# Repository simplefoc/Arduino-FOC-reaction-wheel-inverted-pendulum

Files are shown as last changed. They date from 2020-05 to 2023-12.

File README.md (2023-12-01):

# Arduino field oriented control (FOC) reaction wheel inverted pendulum   



This is a project of designing and controlling the reaction wheel inverted pendulum based entirely on Arduino [SimpleFOC library and SimpleFOC shield](https://github.com/simplefoc/Arduino-FOC). 

<p align="center">
    
    
</p>

This is a very fun project in many ways, and it is intended:
- Students in search for a good testing platform for their advanced algorithms
- Everyone with a bit of free time and a motivation to create something cool :D

### YouTube demonstration video :D
<p align="center">
<a href="https://youtu.be/Ih-izQyXJCI">

</a>
</p>

But for me, the most exciting part of this project was the ability to use the Field Oriented Control algorithm. 
**The main benefits of using the BLDC motor in this project are:**
-  High torque to weight ratio
   - The lighter the better
-  Lots of torque for low angular velocities
   - No need to spin the motor to very high RPM to achieve high torques
-  No gearboxes and backlash
   - Very smooth operation = very stable pendulum

So far, FOC has been restricted to high-end applications due to the complexity and the cost of the hardware mostly, but also due to the lack of user-friendly, well documented software. Therefore I am very happy to show you the projects like this one, which directly benefit the FOC algorithm and BLDC motors and encourage you to use these techniques in your projects as well. One of the very simple ways of starting (demonstrated in this video) is using the [SimpleFOC library and SimpleFOC shield](https://github.com/
/Arduino-FOC). 

## Readme structure 
- [What are the necessary components?](#what-are-the-necessary-components)
  - [3D printed parts](#3d-printed-parts)
  - [Hardware parts](#hardware-parts)
  - [Electrical components](#electrical-components)
    - [BLDC motor](#bldc-motor)
    - [Position sensors](#position-sensors)
    - [BLDC driver](#bldc-driver)
  - [Table mount](#table-mount)
- [Connecting all the components](#connecting-all-the-components)
  - [Encoder 1 (motor)](#encoder-1-motor)
  - [Encoder 2 (pendulum)](#encoder-2-pendulum)
  - [Motor](#motor)
- [Arduino code](#arduino-code)
  - [Encoder 1 (motor) code](#encoder-1-motor-code)
  - [Encoder 2 (pendulum) code](#encoder-2-pendulum-code)
  - [Motor code](#motor-code)
  - [Control algorithm code](#control-algorithm-code)
      - [Stabilization](#stabilization)
      - [Swing-up](#swing-up)
      - [The integration](#the-integration)
  - [Full Arduino code](#full-arduino-code)
- [Contact](#contact)

# What are the necessary components?
Due to the using of the brushless motor and the SimpleFOC shield, this might be one of the simplest hardware setups of the reaction wheel inverted pendulum there is.
<p align="center">
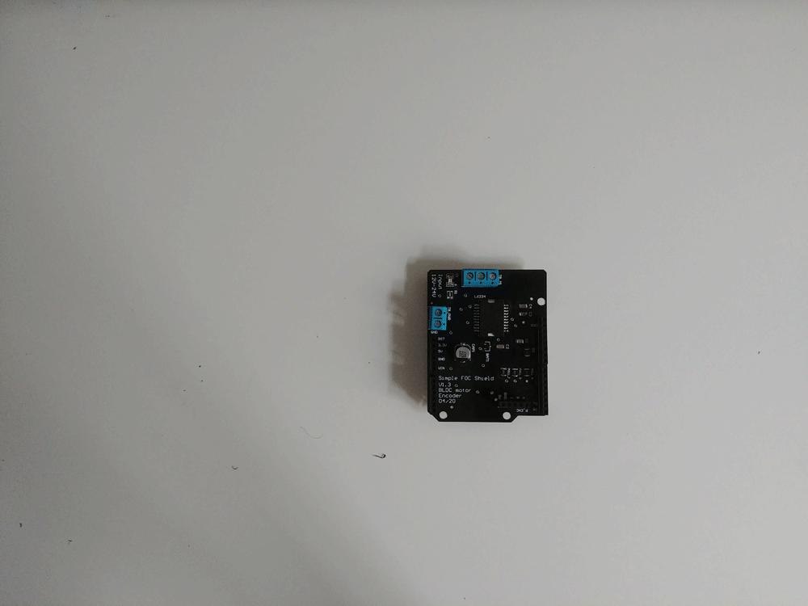
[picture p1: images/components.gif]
    
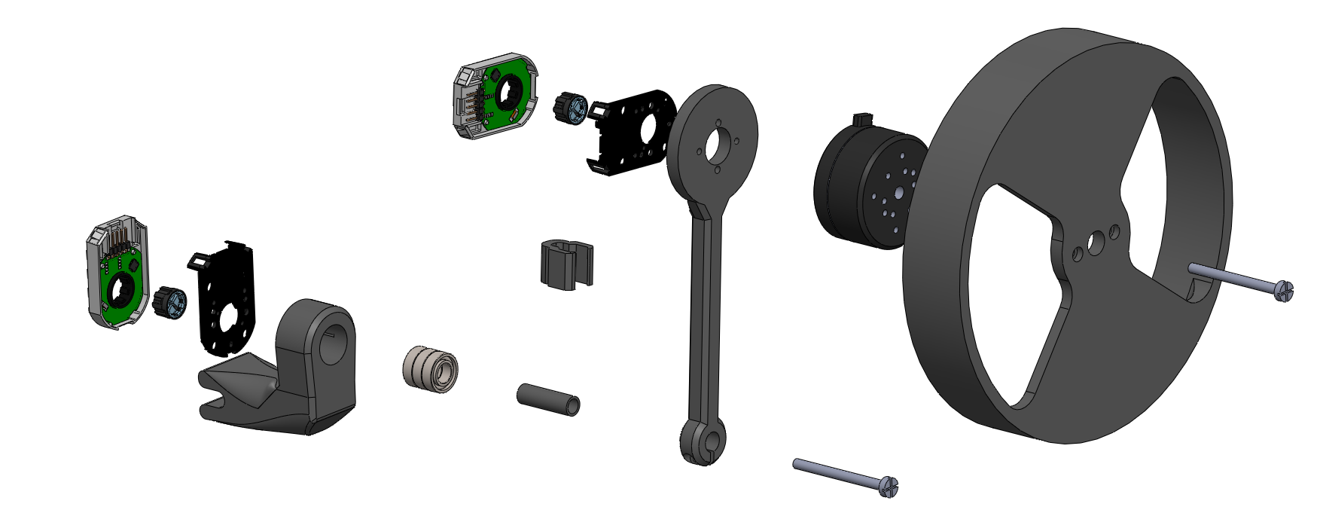
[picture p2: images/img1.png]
    
</p>

## 3D printed parts
This pendulum project has three 3d printed parts. You can find them in the `CAD files > STL` directory. They are:
- inertia wheel (`reaction_wheel.stl`)
    - infill: `70%`
    - layer hight: `<0.12mm`
    - it should be printed as precise as possible (to reduce the vibrations)
    - mass: `100g`
- pendulum arm (`pendulum_arm.stl`) 
    - infill: `50-70%`
    - layer hight: `0.12-0.2mm`
    - no need for too much precision, only the strength
    - mass: `20g`
- base (`bottpm_swingup.stl`)
    - infill: `70%`
    - layer hight: `<0.12`
    - due to the bearings needs to be pretty precise
    - mass: `60g`
- cable holder (`cable_holder.stl`) - *optional*

I have printed the pendulum in the PETG filament but there should be no real difference in using PLA or ABS filaments, this is just what I had in hand at the moment.

You will also find all the CAD files used in this project in the `CAD files` folder. I have included the Solidworks 2016 parts and the full assembly. Additionally all the parts are exported to STEP format for easier porting to the other CAD IDEs.

> Beware: 
I have designed the holes on the pendulum arm and the wheel to match perfectly the motor the encoders I was using, so please check the dimensions of your motors and encoder holes before printing :D

If you would prefer some other CAD format, let me know, maybe I can export it differently. 

## Hardware parts
All of the mechanical hardware is very simple and can be bought in any hardware store. If you prefer to buy it online, I have included links to the Ebay products you could use. 

Component | Description | Link | Price
---- | ---- | ---- | ----
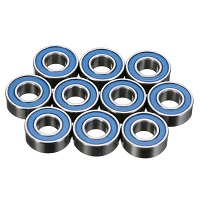
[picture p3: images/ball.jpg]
 | Ball bearing <br> 8x16x5mm <br> 3x | [Ebay](https://www.ebay.com/itm/608-623-625-688zz-Double-sided-Metal-Sealed-Deep-Groove-Ball-Bearing-High-Speed/223959673454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) | 3$
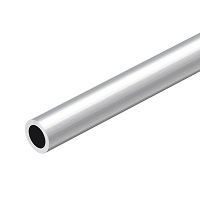
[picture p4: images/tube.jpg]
 | Aluminum tube <br> diameter: 8mm  <br> length: 30mm | [Ebay](https://www.ebay.com/itm/Aluminum-Tube-in-various-diam-and-many-lengths/122904111733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) | 3$
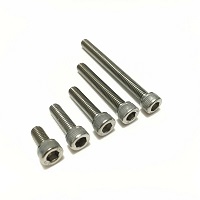
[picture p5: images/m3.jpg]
 |M3 screws<br> 7pcs <br> M3x10mm | [Ebay](https://www.ebay.com/itm/M2-M2-5-M3-M4-M5-M6-M8-Stainless-Steel-Metric-Hex-Socket-Head-Cap-Screws-Bolt/123439613021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) | 2$
 | M4 screws & nuts<br> 2pcs <br> M4x50mm | [Ebay](https://www.ebay.com/itm/M2-M2-5-M3-M4-M5-M6-M8-Stainless-Steel-Metric-Hex-Socket-Head-Cap-Screws-Bolt/123439613021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) | 4$

## Electrical components
### BLDC motor
Unfortunately the BLDC motor I was using in my video is an old version of the [iPower GM4108](https://shop.iflight-rc.com/index.php?route=product/product&product_id=217&search=GM4108H-120T) motor which is not available anymore to buy, in any case I was not able to find a website that would sell them. 
The good news is that you can use basically any other gimbal motor in that class with only minor modifications, mostly in the CAD parts - change the mounting holes positions. Some of the motors I was able to find that would be the most similar to my motor would be:
Component | Description | Link | Price
---- | ---- | ---- | ----
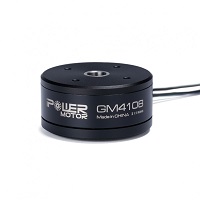
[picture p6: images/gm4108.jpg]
 | iPower Motor GM4108H-120T | [iFlight webshop](https://shop.iflight-rc.com/index.php?route=product/product&product_id=217&search=GM4108H-120T) | 35$
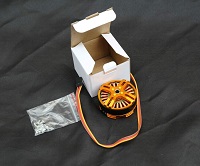
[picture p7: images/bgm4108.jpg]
 | BGM 4108 120T | [Ebay](https://www.ebay.com/itm/gimbal-brushless-motor-BGM-4108-120T-hollow-silver-version/261539739163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) | 30$
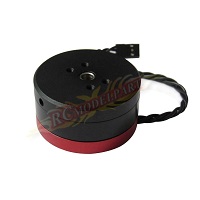
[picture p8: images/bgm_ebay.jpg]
 | BGM4108-150HS | [Ebay](https://www.ebay.com/itm/New-Brushless-Gimbal-Motor-BGM4108-150HS-24N22P-for-Sony-NEX5-7-Camera-Mount-DIY/261903969970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) | 32$

### Position sensors
In this project I am using two encoders to track the movement of the pendulum and the motor. Now, this is somewhat particular to my implementation, there are may ways to measure the angle of the pendulum. You could use the `IMU` and measure the inclination by combining the accelerometer and the gyro measurement, you could also use the magnetic sensors such as `AS5048` and similar absolute encoders. 

The encoders I have used in this project are:
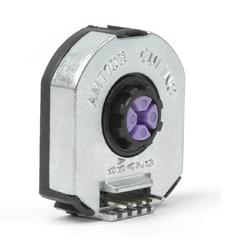
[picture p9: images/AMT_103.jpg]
 | AMT103 CUI | [Mouser](https://eu.mouser.com/ProductDetail/CUI-Devices/AMT103-V?qs=WyjlAZoYn51X2GCrrvGQTg==T) | 20$
---- | ---- | ---- | ----

The main features these encoders are:
 - Configurable number of impulses per revolution (PPR)
    - `48 - 2048`
 - Vey easy mounting
    - click-on to any type of shaft ` < 8mm`
 - Integrated pull-ups 
 - Index pin
 - Low-cost `~20$`

### BLDC driver
In this project I used the [SimpleFOCShield board](https://docs.simplefoc.com/arduino_simplefoc_shield_showcase) which is basically an Arduino shield which enables the usage of the FOC algorithm with the BLDC motors. It is practically plug & play in combination with the Arduino [SimpleFOC library](https://docs.simplefoc.com/arduino_simplefoc_library_showcase).

There are quiet a few boards out there that are in short a triple H-bridge motor drivers and the SimpleFOC library will be compatible with most of them. But for most of them the hardware setup will be a bit more complex. Here are some examples of the possible BLDC drives you could use:
Examples | Description | Link | Price
---- | ---- | ---- | ---
[](https://simplefoc.github.io/simplefoc_shield_product)| Arduino SimpleFOCShield | [More info](https://simplefoc.github.io/simplefoc_shield_product) | 25$
[](https://www.ebay.com/itm/L6234-Breakout-Board/153204519965?hash=item23abb3741d:g:LE4AAOSwe35bctgg) | Dorotek L6234 breakout board| [Drotek](https://store-drotek.com/212-brushless-gimbal-controller-l6234.html), [Ebay](https://www.ebay.fr/itm/L6234-Breakout-Board-/153204519965) | 30$
[](https://www.ebay.com/itm/HMBGC-V2-0-3-Axle-Gimbal-Controller-Control-Plate-Board-Module-with-Sensor/351497840990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) | HMBGC V2.2 | [Ebay](https://www.ebay.com/itm/HMBGC-V2-0-3-Axle-Gimbal-Controller-Control-Plate-Board-Module-with-Sensor/351497840990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) | 20$

## Table mount
There are surely many ways to mount this pendulum to the stable surface, in my case I hade on my hands a very robust vacuum suction cup holder which works perfectly for this application. It is not the cheapest solution though.
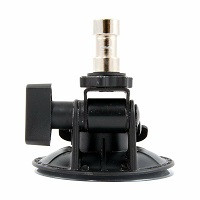
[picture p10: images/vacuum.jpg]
 | Delkin Fat Gecko | [Ebay](https://www.ebay.com/itm/Delkin-Fat-Gecko-Stealth-Vacuum-Light-Mount-Holds-4-LB-Free-US-Shipping/141019370583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) | 30$
---- | ---- | ---- | ----

The only important thing is that the pendulum base is fixed, everything else is the design choice :D 

# Connecting all the components
In this project all the electronics components are:

[Arduino UNO](https://store.arduino.cc/arduino-uno-rev3) | [Arduino <span class="simple">Simple<span class="foc">FOC</span>Shield</span>](arduino_simplefoc_shield_showcase) | 2x [AMT 103 encoder](https://www.mouser.fr/ProductDetail/CUI-Devices/AMT103-V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) | [iPower GM4108-120T](https://shop.iflight-rc.com/index.php?route=product/product&product_id=217&search=GM4108H-120T)
--- | --- | --- | --- 
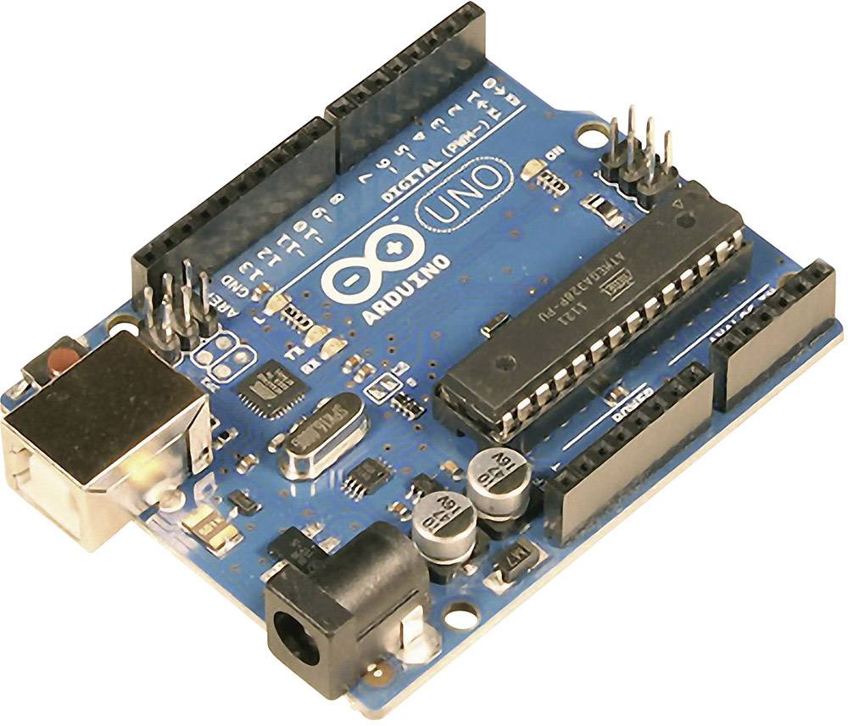
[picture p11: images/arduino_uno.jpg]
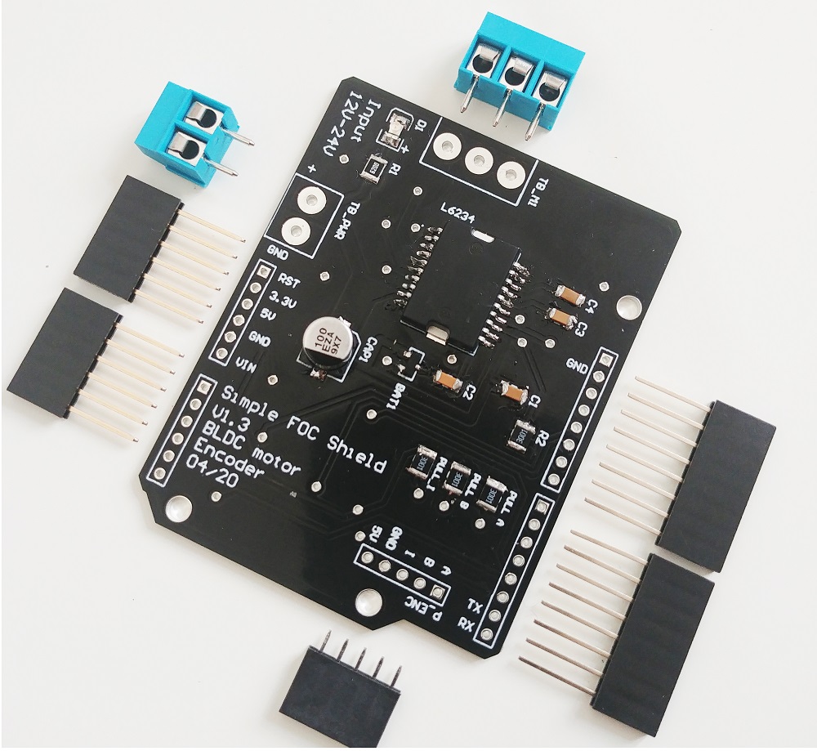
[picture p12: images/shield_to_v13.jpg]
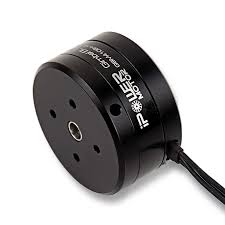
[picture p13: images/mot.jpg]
 |    |   |  

## Encoder 1 (motor)
- Channels `A` and `B` are connected to the encoder connector `P_ENC`, terminals `A` and `B`. 

## Encoder 2 (pendulum)
<blockquote > Pinout restriction<br>
Arduino UNO doesn't have enough hardware interrupt pins for two encoders therefore we need to use the software interrupt library. </blockquote>

- Encoder channels `A` and `B` are connected to the pins `A0` and `A1`.

## Motor
- Motor phases `a`, `b` and `c` are connected directly the motor terminal connector `TB_M1`

<blockquote>Alignment<br> Motor phases <code>a</code>,<code>b</code>,<code>c</code> and encoder channels <code>A</code> and <code>B</code> have to have the same orientation for the algorithm to work. But don't worry about it too much. Connect it initially as you wish and then if the motor locks in place reverse phase <code>a</code> and <code>b</code> of the motor, that should be enough.
</blockquote>

# Arduino code 
Let's go through the full code for this project and write it together.
First thing you need to do is include the `SimpleFOC` library:

```cpp
#include <SimpleFOC.h>
```
Make sure you have the library installed. If you still don't have it please check the [get started page](getting_started).

Also in this case, we are using two encoders so we will need to have a software interrupt library.
I would suggest using `PciManager` library. If you have not installed it yet, you can do it using the Arduino library manager directly. Please check the *SimpeFOClibrary*'s `Encoder` class [docs](https://simplefoc.github.io/Arduino-FOC/encoder) for more info.
So once you have it please include it to the sketch:
```cpp
// software interrupt library
#include <PciManager.h>
#include <PciListenerImp.h>
```

## Encoder 1 (motor) code 

First we define the `Encoder` class with the A and B channel pins and number of impulses per revolution.
```cpp
// define Encoder
Encoder encoder = Encoder(2, 3, 500);
```
Then we define the buffering callback functions.
```cpp
// channel A and B callbacks
void doA(){encoder.handleA();}
void doB(){encoder.handleB();}
```
In the `setup()` function we initialize the encoder and enable interrupts:
```cpp
  // initialize encoder hardware
  encoder.init();
  // hardware interrupt enable
  encoder.enableInterrupts(doA, doB);
```
And that is it, let's setup the pendulum encoder.

<blockquote class="info">For more configuration parameters of the encoders please check the *SimpeFOClibrary*'s <code>Encoder</code> class <a href="https://docs.simplefoc.com/encoder">docs</a>.</blockquote>

## Encoder 2 (pendulum) code
We define the pendulum as the `Encoder` class with the A and B channel pins and number of impulses per revolution.
```cpp
// define Encoder
Encoder pendulum = Encoder(A0, A1, 1000);
```
Then we define the buffering callback functions.
```cpp
// channel A and B callbacks
void doPA(){pendulum.handleA();}
void doPB(){pendulum.handleB();}
```
Next we define the `PciManager` pin change listeners:
```cpp
// pin change listeners
PciListenerImp listenerPA(pendulum.pinA, doPA);
PciListenerImp listenerPB(pendulum.pinB, doPB);
``` 
In the `setup()` function first we initialize the pendulum encoder:
```cpp
  // initialize encoder hardware
  pendulum.init();
```
And then instead of calling `pendulum.enableInterrupt()` function we use the `PciManager` library interface to attach the interrupts.
```cpp
  // interrupt initialization
  PciManager.registerListener(&listenerPA);
  PciManager.registerListener(&listenerPB);
```
And that is it the pendulum is ready, let's setup the motor.

## Motor code
First we need to define the `BLDCMotor` class with the number of pole pairs(`11`) of the motor.

```cpp
// define BLDC motor
BLDCMotor motor = BLDCMotor(11);
```
<blockquote class="warning">If you are not sure what your pole pairs number is please check the  <code>find_pole_pairs.ino</code> example.</blockquote>

Next we need to define the `BLDCDriver3PWM` class with the PWM pin numbers and the driver enable pin.
```cpp
// define BLDC driver
BLDCDriver3PWM driver = BLDCDriver3PWM(9, 10, 11, 8);
```

Then in the `setup()` we configure first the voltage of the power supply if it is not `12` Volts and initialize and link the driver.
```cpp
  // power supply voltage
  // default 12V
  driver.voltage_power_supply = 12;
  driver.init();
  motor.linkDriver(&driver);
```
Then we tell the motor which control loop to run by specifying the `motor.controller` variable.
```cpp
  // set control loop type to be used
  // MotionControlType::torque
  // MotionControlType::velocity
  // MotionControlType::angle
  motor.controller = MotionControlType::torque;
```
<blockquote class="info">For more information about the voltage control loop please check the  <a href="voltage_loop">doc</a>.</blockquote>

Next we connect the encoder to the motor, do the hardware init and init of the Field Oriented Control.
```cpp  
  // link the motor to the sensor
  motor.linkSensor(&encoder);

  // initialize motor
  motor.init();
  // align encoder and start FOC
  motor.initFOC();
```
The last peace of code important for the motor is of course the FOC routine in the `loop` function.
```cpp
void loop() {
  // iterative FOC function
  motor.loopFOC();

  // iterative function setting and calculating the angle/position loop
  // this function can be run at much lower frequency than loopFOC function
  motor.move(target_voltage);
}
```
Now we are able to read the two encoders and set the voltage to the motor, now we need to write the stabilization algorithm.
<blockquote class="info">For more configuration parameters and control loops please check the *SimpleFOClibrary*'s <code>BLDCMotor</code> class <a href="https://docs.simplefoc.com/motor_initialization">doc</a>.</blockquote>

## Control algorithm code

The control algorithm is divided in two stages. Stabilization and swing-up.

#### Stabilization

In order to stabilize the pendulum we will be using a state space controller which means that it takes in consideration all three variables important for this pendulum system:
- pendulum angle - `p_angle`
- pendulum velocity - `p_vel`
- motor velocity - `m_vel`

The controller code is very simple at the end, it just calculates the linear control rule:
```cpp
target_voltage =  40*p_angle + 7*p_vel + 0.3*m_vel;
```
The gains `40`,`7` and `0.3` you can imagine as weights, which tell how much we care about these variables. The highest weight is obviously on the pendulum angle and the smallest is on motor velocity that makes sense. Basically if we set `0` to the motor velocity weight, your pendulum will still be stable but your motor will probably never stop spinning. It will always have some velocity. On the other hand if you put it much higher, you will probably prioritize your motor movements over the stability and your pendulum will no longer be stable. So there is a tradeoff here. 

This is a very simple explanation of a relatively complex topic and I would like to point you toward a nice [youtube video](https://www.youtube.com/watch?v=E_RDCFOlJx4) explanation of similar approaches.

Also maybe interesting to say is that for a system like this one there is really no need to run it with the sample times less then 20ms. In my case I have run it at ~25ms, but you can go even to 50ms.

<blockquote class="warning"><b>NOTE</b><br> The FOC algorithm <code>motor.loopFOC()</code> will run ~1ms but the control algorithm and the function <code>motor.move()</code> will be downsampled to ~25ms.</blockquote>

#### Swing-up

The swingup implemented in this example is the simples one possible, that is always good, it means that the hardware is well designed so you dont need to make some fancy algorithm to make it work :D

This is hte code of the swing-up:
```cpp
target_voltage = -_sign(pendulum.getVelocity())*motor.voltage_power_supply*0.4;
```
What it does really is it checks which direction the pendulum is moving `sign(pendulum.getVelocity())` and sets the very high voltage value `motor.voltage_power_supply*0.4` in the opposite direction (`-`). 
It means that the algorithm is going to try to accelerate the movement of the pendulum (because the pendulum acceleration is caused as the reaction of the motor acceleration, but inverse direction).
The voltage value you are setting is something you will tune. I have found that for my pendulum 40% of the maximum voltage was enough to make the pendulum swing up. More voltage would make it swing up too fast and the pendulum would not be able to stabilize when it reaches the top. Much less voltage would not be enough for the pendulum to swing up at all.

#### The integration

Now we jsut need to decide when do we do the swing up and when do we do the stabilization. Basically we need to decide the angle from which we decide that it is not possible to recover and we should proceed with the swing-up. 
I my case I have decided it is `0.5 radians`, `~30degrees`. 

So the full control algorithm code looks like this:
```cpp
// control loop each ~25ms
  if(loop_count++ > 25){
    
    // calculate the pendulum angle 
    float pendulum_angle = constrainAngle(pendulum.getAngle() + M_PI);

    float target_voltage;
    if( abs(pendulum_angle) < 0.5 ) // if angle small enough stabilize
      target_voltage =  40*pendulum_angle + 7*pendulum.getVelocity() + 0.3*motor.shaftVelocity();
    else // else do swing-up
      // sets 40% of the maximal voltage to the motor in order to swing up
      target_voltage = -_sign(pendulum.getVelocity())*motor.voltage_power_supply*0.4;

    // set the target voltage to the motor
    motor.move(target_voltage);

    // restart the counter
    loop_count=0;
  }
```
And that is it guys we can read our pendulum angle, we can control the motor, and we have our control algorithm. Lets write the full code! 

## Full Arduino code

For the full code I have just added a function `constrainAngle()` to constrain the pendulum angle in between -180 and 180 degrees and moved the stabilization part of the controller to the stand-alone function `controllerLQR()`.

```cpp
#include <SimpleFOC.h>
// software interrupt library
#include <PciManager.h>
#include <PciListenerImp.h>

// BLDC motor init
BLDCMotor motor = BLDCMotor(11);
// driver instance
BLDCDriver3PWM driver = BLDCDriver3PWM(9, 10, 11, 8);
//Motor encoder init
Encoder encoder = Encoder(2, 3, 500);
// interrupt routine 
void doA(){encoder.handleA();}
void doB(){encoder.handleB();}

// pendulum encoder init
Encoder pendulum = Encoder(A1, A2, 1000);
// interrupt routine 
void doPA(){pendulum.handleA();}
void doPB(){pendulum.handleB();}
// PCI manager interrupt
PciListenerImp listenerPA(pendulum.pinA, doPA);
PciListenerImp listenerPB(pendulum.pinB, doPB);

void setup() {
  
  // initialise motor encoder hardware
  encoder.init();
  encoder.enableInterrupts(doA,doB);
  
  // init the pendulum encoder
  pendulum.init();
  PciManager.registerListener(&listenerPA);
  PciManager.registerListener(&listenerPB);
  
  // set control loop type to be used
  motor.controller = MotionControlType::torque;

  // link the motor to the encoder
  motor.linkSensor(&encoder);
  
  // driver
  driver.voltage_power_supply = 12; 
  driver.init();
  // link the driver and the motor
  motor.linkDriver(&driver);

  // initialize motor
  motor.init();
  // align encoder and start FOC
  motor.initFOC();
}

// loop downsampling counter
long loop_count = 0;

void loop() {
  // ~1ms 
  motor.loopFOC();

  // control loop each ~25ms
  if(loop_count++ > 25){
    // updating the pendulum angle sensor
    // NECESSARY for library versions > v2.2 
    pendulum.update();
    // calculate the pendulum angle 
    float pendulum_angle = constrainAngle(pendulum.getAngle() + M_PI);

    float target_voltage;
    if( abs(pendulum_angle) < 0.5 ) // if angle small enough stabilize
      target_voltage = controllerLQR(pendulum_angle, pendulum.getVelocity(), motor.shaftVelocity());
    else // else do swing-up
      // sets 40% of the maximal voltage to the motor in order to swing up
      target_voltage = -_sign(pendulum.getVelocity())*motor.voltage_limit*0.4;

    // set the target voltage to the motor
    motor.move(target_voltage);

    // restart the counter
    loop_count=0;
  }

}

// function constraining the angle in between -pi and pi, in degrees -180 and 180
float constrainAngle(float x){
    x = fmod(x + M_PI, _2PI);
    if (x < 0)
        x += _2PI;
    return x - M_PI;
}

// LQR stabilization controller functions
// calculating the voltage that needs to be set to the motor in order to stabilize the pendulum
float controllerLQR(float p_angle, float p_vel, float m_vel){
  // if angle controllable
  // calculate the control law 
  // LQR controller u = k*x
  //  - k = [40, 7, 0.3]
  //  - x = [pendulum angle, pendulum velocity, motor velocity]' 
  float u =  40*p_angle + 7*p_vel + 0.3*m_vel;
  
  // limit the voltage set to the motor
  if(abs(u) > motor.voltage_limit*0.7) u = sign(u)*motor.voltage_limit*0.7;
  
  return u;
}
```
This is the full code guys. You can also find it in the `Arduino` directory of the git repo. 

I hope you found this readme (even though very long) helpful and I hope you will be successful in realizing this project as well. It is very very cool! 

# Contact
Feel free to leave the issue if you experience any problems setting up this project!

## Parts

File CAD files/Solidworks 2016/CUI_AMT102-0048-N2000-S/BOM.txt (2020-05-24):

3DX_CUI_Supplier: CUI, Inc
3DX_CUI_Description: AMT10 Radial, Fixed Resolution, 48 PPR, 8 Index Pulses, 2 mm Bore, Standard, Incremental, Capacitive Modular Encoder
3DX_CUI_Model Number: AMT102-0048-N2000-S

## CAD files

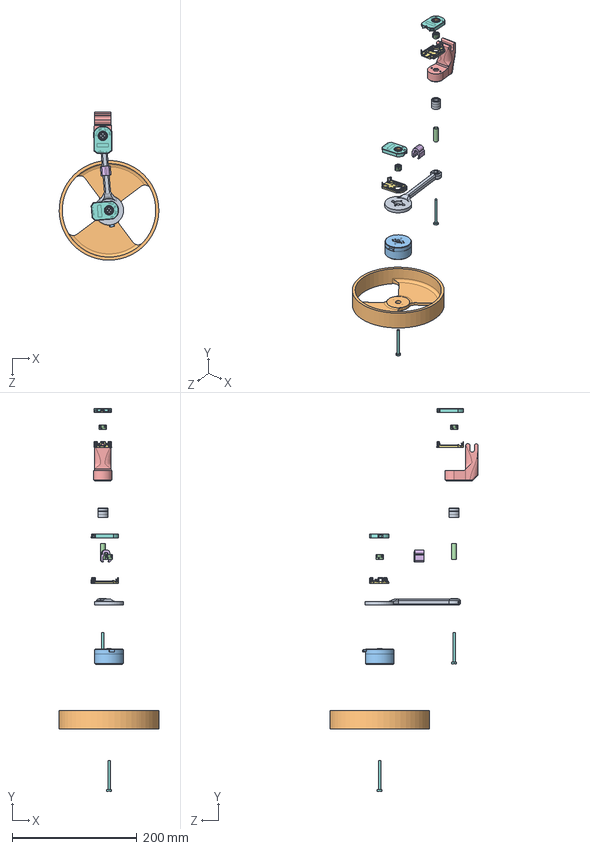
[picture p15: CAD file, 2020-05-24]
CAD files/Solidworks 2016/inverted_inertia_pendulum.SLDASM
159.9 x 614.7 x 238.1 mm
pendulum_arm
reaction_wheel
motor
shaft
bottom_swingup
cable_holder
CUI_amt-102-base-rev-k x 2
CUI_amt-102-top-cover-rev-h x 2
CUI_amt-sleeve-rev-d( 2 mm) x 2
CUI_amt-hub-top-rev-d1 x 2
CUI_amt-hub-bottom-rev-b x 2
CUI_amt10x-shaft-adaptor-rev-e x 2
CUI_receiver-board x 2
CUI_rotor-board-rev f x 2
CUI_transmitter-board amt10(amt-102) x 2
m4_screw x 2
radial ball bearing_68_iso x 3

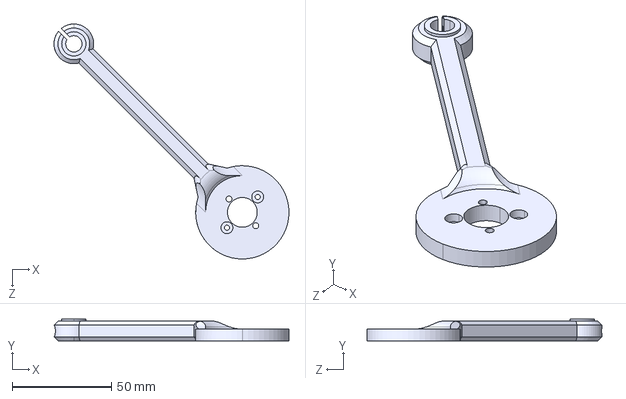
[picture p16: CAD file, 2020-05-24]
CAD files/STEP/pendulum_arm.STEP
118.4 x 11.0 x 118.4 mm

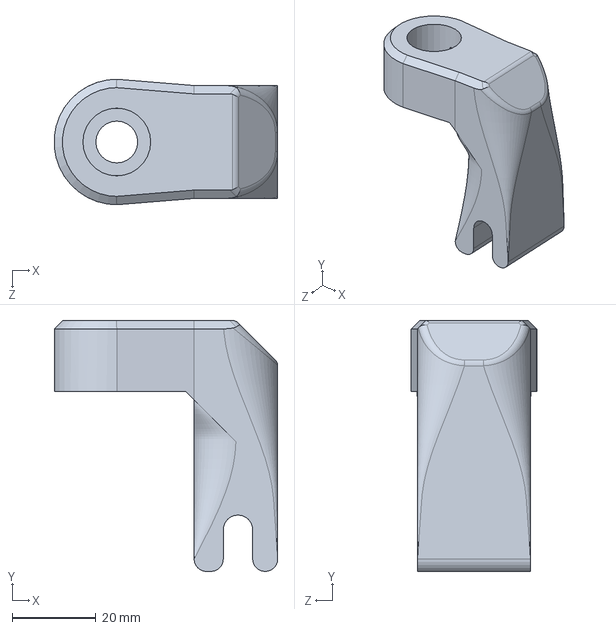
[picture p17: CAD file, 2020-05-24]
CAD files/Solidworks 2016/bottom_swingup.SLDPRT
53.4 x 60.0 x 30.0 mm

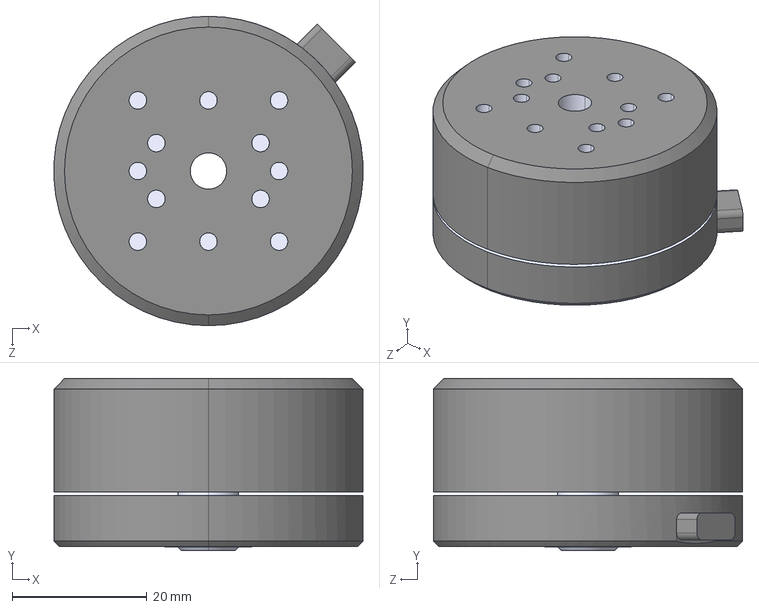
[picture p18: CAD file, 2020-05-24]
CAD files/STEP/motor.STEP
45.9 x 25.6 x 46.0 mm

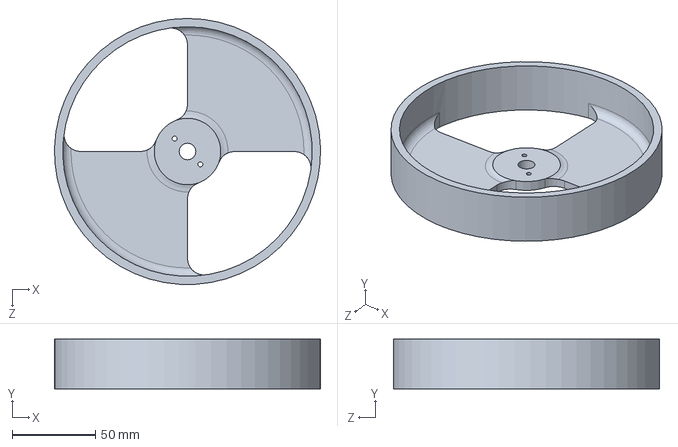
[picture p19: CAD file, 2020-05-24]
CAD files/Solidworks 2016/reaction_wheel.SLDPRT
159.9 x 30.0 x 160.0 mm

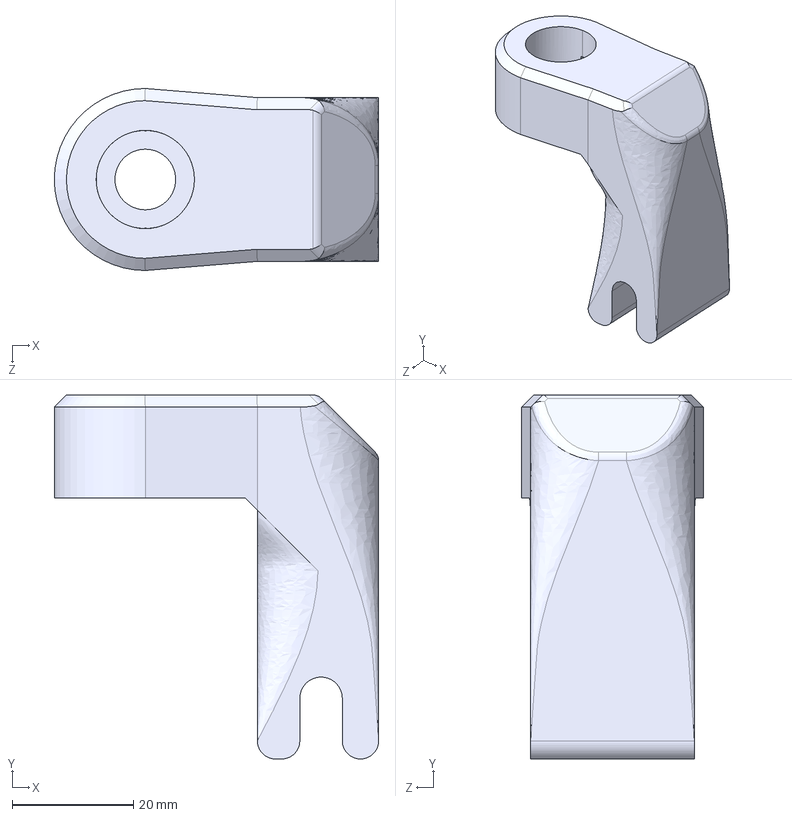
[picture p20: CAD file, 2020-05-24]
CAD files/STEP/bottom_swingup.STEP
53.5 x 60.0 x 30.0 mm

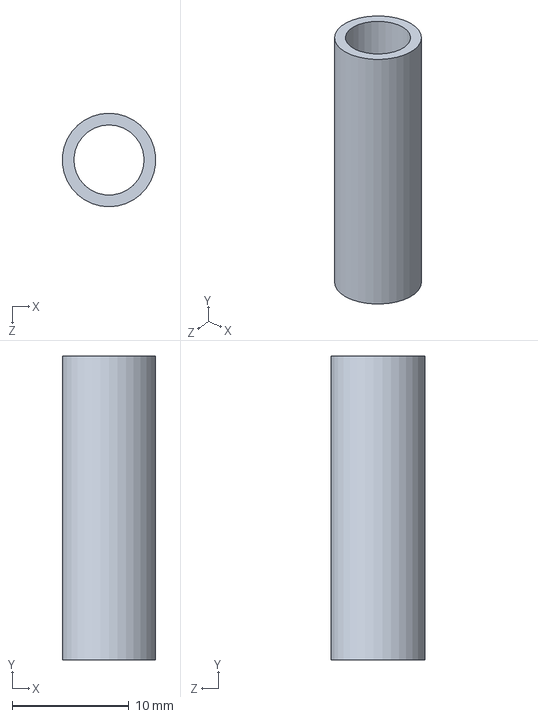
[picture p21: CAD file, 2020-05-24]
CAD files/Solidworks 2016/shaft.SLDPRT
7.97 x 26.0 x 8.00 mm

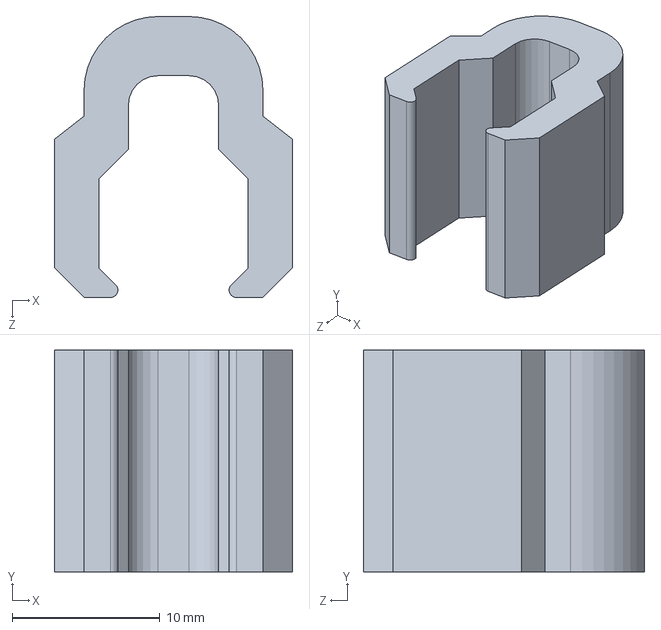
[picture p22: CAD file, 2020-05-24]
CAD files/Solidworks 2016/cable_holder.SLDPRT
16.1 x 15.0 x 19.0 mm

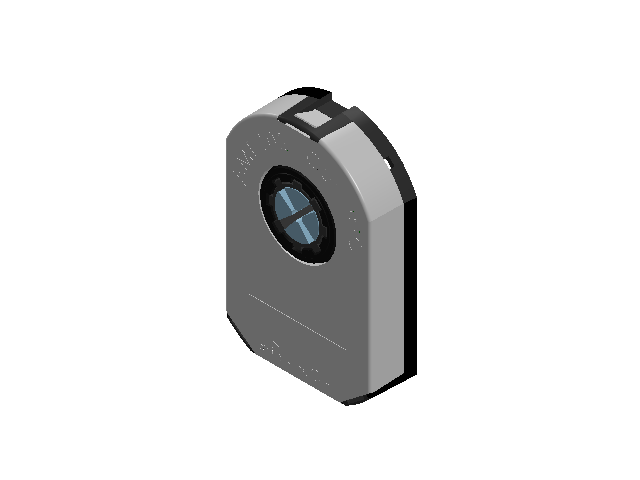
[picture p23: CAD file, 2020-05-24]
CAD files/Solidworks 2016/CUI_AMT102-0048-N2000-S/CUI_cui_amt102-0048-n2000-s.sldasm
CUI_amt-102-base-rev-k
CUI_amt-102-top-cover-rev-h
CUI_amt-sleeve-rev-d( 2 mm)
CUI_amt-hub-top-rev-d1
CUI_amt-hub-bottom-rev-b
CUI_amt10x-shaft-adaptor-rev-e
CUI_receiver-board
CUI_rotor-board-rev f
CUI_transmitter-board amt10(amt-102)

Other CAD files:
CAD files/Solidworks 2016/CUI_AMT102-0048-N2000-S/CUI_amt-hub-top-rev-d1.sldprt
CAD files/Solidworks 2016/CUI_AMT102-0048-N2000-S/CUI_amt-sleeve-rev-d( 2 mm).sldprt
CAD files/Solidworks 2016/CUI_AMT102-0048-N2000-S/CUI_receiver-board.sldprt
CAD files/Solidworks 2016/CUI_AMT102-0048-N2000-S/CUI_amt10x-shaft-adaptor-rev-e.sldprt
CAD files/STEP/reaction_wheel.STEP
CAD files/STEP/cable_holder.STEP
CAD files/Solidworks 2016/CUI_AMT102-0048-N2000-S/CUI_amt-102-base-rev-k.sldprt
CAD files/Solidworks 2016/pendulum_arm.SLDPRT
CAD files/Solidworks 2016/CUI_AMT102-0048-N2000-S/CUI_amt-hub-bottom-rev-b.sldprt
CAD files/STL/bottom_swingup.STL
CAD files/STL/cable_holder.STL
CAD files/STL/pendulum_arm.STL
CAD files/STL/reaction_wheel.STL
CAD files/Solidworks 2016/CUI_AMT102-0048-N2000-S/CUI_amt-102-top-cover-rev-h.sldprt
CAD files/Solidworks 2016/CUI_AMT102-0048-N2000-S/CUI_rotor-board-rev f.sldprt
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

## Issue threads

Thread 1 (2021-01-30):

2nd encoder connection

shiftux, 2021-01-30:
hello
first off, thanks for the amazing documentation on your cool project!! - great work!
looking to build something similar...
there is 1 thing i don't understand in your setup: the foc-shield, as i understand it, does only allow 1 encoder to be connected to it. you obviously need 2. now i know the shields could be stackable, but you don't seem to stack them...
how did you solve that? - repurposing free pins? is that then still compatible with the foc library?
thanks!

askuric, 2021-01-30:
Hey @shiftux

Yes, the connector for encoder is there more for convenience reasons really. And it provides you a way to use the integrated pull-ups if you need ones. But most of the common encoders do not need any and you can just plug them directly to any digital pin.

So you can really do the same thing by plugging encoder ground and 5V to Arduino ground and 5v,  And then the a,b and z to the any free Arduino digital pin.  :D

shiftux, 2021-01-30:
ok, i figured, thanks! :)

Closed 2021-01-30.

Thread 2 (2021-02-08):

debug foc board

shiftux, 2021-02-08:
hello

I got a foc board and was looking to try out an inverted pendulum.
As a first step I'm trying out the 2V motor rotation (beginning of your video), however I don't get the motor initialisation and there is no movement.

Trying to debug this there are a couple of things that seem odd to me:
- when I power the foc shield with 12V, the arduino does not get powered. is that normal? - the foc shield gets a blue led on, so there should be power. the normal Vin pin on the arduino works when I supply it with 5V
- when using the foc library, i don't seem to be able to get a serial connection, at least i don't see anything printed on it. is that intended? - this works on the arduino normally.
- also in the code you specify pins on the arduino. however i did not find a mapping of which pins connect where on the shield. for example the encoder pins (the 5 solo pins on the board), how do I know which pins they are connected to on the board?
- with older versions of the arduino mega the 2 front most pins on both sides are not connected (SCL/SDA on the right side and GND+IOREF on the left) does the foc shield rely on the IOREF pin?
- on the [bldc driver class](https://docs.simplefoc.com/bldcdriver3pwm#bldc-driver-3pwm---bldcdriver3pwm) there is an "enable pin" (default 8) mentioned. However there is no explanation to it. do i need to force this pin to 5V or to GND for the driver to work?

thanks for your pointers

my hardware:
board: arduino mega 1280
motor: https://www.aliexpress.com/item/4001296350749.html
encoder: https://www.aliexpress.com/item/32990323362.html
(it's the first time i'm using this type of encoder, i didn't find any info on pull-up/down, so i didn't solder any of those on the board)

shiftux, 2021-02-09:
@askuric
Thanks for your detailed explanation! - This helped!

Indeed I did not read enough of the documentation. I read the phrase `All the Arduino SimpleFOCShield boards will be initially tested and they will be shipped with initial configuration` in the doc you linked and from that I concluded that all the solder pads were just there to CHANGE something from the default config. I didn't understand that the pwm and encoder pin selectors needed to be soldered in any case.

I got the motor to spin at 2V speed (voltage controlled) in a very simple setup. So I'm confident the rest will work.

Serial connection does in fact work, I just did not realize that the FOC init functions took that long :) after that I get output.

I think what would have helped me to understand the wiring is a diagram like the one I attached. This makes it clear for me to see what pins are used and exposed where on the board.
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

The only issues that remain for me are:
- The power supply to the board I did not get to work with a jumper cable from 5V to VIN...
- When I have the shield attached, I can not program the Arduino. I get an error: `avrdude: stk500_paged_write(): (a) protocol error, expect=0x14, resp=0x10`. Is there something connected to the TX/RX pins??
- The encoders I got lack a bit of documentation. I am not sure if I need pull up/down resistors for those. Would you know how I could find that out?

Thanks for your help!

askuric, 2021-02-09:
Hey @shiftux ,

You are indeed completely right!
I will make sure to update the docs, and I stopped shipping the boards with the initial configuration due to the  fact that the conductive ink I use for testing somehow made people more confused than it actually helped :D

Ok its great to hear that you actually have voltage control. This is basically all you need for the project of inverted pendulum. Is you mega1280 making a lot of noise? It should not have high frequency pwm signal, you should be able to hear the wining quiet loudly?

- Which board version do you have? Is it v1 or v2? Does the board have the voltage regulator, only the v2.0+ have the voltage regulator, the earlier versions will not power your Arduino.
- There is nothing connected to the pins `D0` and `D1`, I am not sure why this happens! I did not have such problems so far really, I will look into it and I'll let you know as soon as I find something out. Did you try to disconnect the motor and when you program the board?
- You could measure the resistance in between `A`,`B` pins and `5V` pin of the encoder. If it has cca 1-5kOhm resistance it already has a pull-up.  But if the encoder works in voltage mode, you are probably all set, usually if they need the pull-up they will not work at all before you enable it.

Let me know how it goes :D

shiftux, 2021-02-10:
@askuric,

Again, thanks for the detailed answer!

I'm using the FOC shield V1.3.3. I also tried it with an Arduino Uno now, but still no power over the VIN pin. Must be related to the version of the board as you mentioned.
Also the upload works better with the Arduino Uno, compared to what I mentioned with the mega.
Regarding the encoders, I don't measure a resistance between 5V and the A/B signal. But I did find the datasheet, where it is mentioned that there is a 2.5kO on the output, so I didn't solder anything.

All in all the electronics and circuit are OK now and working for the pendulum example.
After tuning the LQR constants a bit i get a beautifully stabilized pendulum!
 thanks for your help!
(OK for me to close this issue)

askuric, 2021-02-14:
Hey @shiftux ,

Sorry for a late response!

Yes version 1.3.3 does not have the voltage regulators, the versions v2.0+ do have them.

I'm really happy that you have made it work and that you're satisfied with the results. :D

Unstable dynamical systems are a passion of mine and each time I am able to make one of them stable using the magic of control algorithms it makes me a happy man.
And being able to share this project with other people just completed the experience.

Cheers!

shiftux, 2021-02-14:
Hehe the thanks goes to you!
Very easy to get it done with all your documentation and quick help on
github.
If I have some more time I'll try a few different control strategies. And
inertia configurations...
Best

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

Closed 2021-02-12.

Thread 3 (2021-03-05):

Can this be achieved using a gyro?

athix, 2021-03-05:
Is it possible to achieve a similar result, but instead of using an encoder to get the position of the pendulum, use a gyro like the BNO055?

I'm trying to create a balancing RC vehicle that uses a reaction wheel to keep itself upright, but struggling to find a good motor/ESC pair, and came across the Arduino FOC project which seems promising. From what I can tell, it includes torque control, which is exactly what I would need.

askuric, 2021-03-05:
Hey @athix ,
Yes sure. You can replace the encoder with the imu and read the angle and angular velocity. The IMU in not integrated in the library at the moment and you'll need to use an external library for to make it work. But there should not be any big issues. There has been a few of these pendulums using the imu already, especially by [rem-rc](https://m.youtube.com/user/ReM555)

You can see the SimpkeFOC balancer project for an implemetation of stabilisation using the IMU.

athix, 2021-03-05:
Ahh, excellent! Thanks for pointing me in the right direction @askuric. :smile:

I actually circled back to the ArduinoFOC after seeing Rem-RC comment on a video about using it for his projects, but I wasn't sure if there was a public code example to use as a base. I'll look into combining the reaction wheel control with the balancing bot IMU input.

One other question I would have is if it's possible to use typical drone BLDC motors, or if you're limited to the gimbal type motors I've seen on most of the Arduino-FOC projects. The project that I'm envisioning would be on the more to medium-to-high power end of the scale, and the motors I've seen for most of these projects wouldn't provide enough torque I imagine. I'm guessing that this is primarily limited by the power distribution board that would sit between the arduino and the motor? I have a cheap little BLDC motor and L298N that I could use at the moment, but I couldn't find the ArduinoFOC shield on any of the usual online stores. Is that something where I would have to order the circuit-board itself, all the SMD components, and solder the parts on myself? I looked at the documentation for supported parts, but ended up getting a bit confused.

As for the IMU integration, would it be sensible to look at the [source code from Adafruit](https://github.com/adafruit/Adafruit_BNO055/blob/master/Adafruit_BNO055.cpp) and use that to implement support within the ArduinoFOC library? If so, I can focus on adding support for the BNO055 instead of doing the conversion specifically within my own code.

athix, 2021-03-05:
Ah, it looks like the primary benefit of the gimbal motors is that they have encoders already built in due to being designed to hold a specific angle? In that case, it may make sense for me to start with a gimbal motor for now, then move up to integrating my own BLDC motor and encoder pair when my power requirements increase?

New to engineering, so still learning about how all this stuff integrates together.

athix, 2021-03-09:
For those in the future, it looks like you can indeed use the L298N as the motor driver. Still searching on the gimbal motor/motor encoder however. If I find a solution I'll follow up with it here.

athix, 2021-03-16:
* Gimbal motor with encoder
  * `IFlight iPower GM2804H-100T GM2804 Brushless Gimbal Motor with AS5048A Encoder/Aluminum Case for camera stabilizing systems`
  * [AliExpress Link](https://www.aliexpress.com/item/1005001809310761.html)
* Gimbal motor driver board (recommended by RemRC/Rem666)
  * `2 Axis BGC MOS 3.0 Large Current Brushless Gimbal Controller Board Driver Alexmos Simple Simple BGC Two-axis`
  * [AliExpress Link](https://www.aliexpress.com/item/32861412984.html)

Closed 2021-03-09.

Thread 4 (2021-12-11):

Mounting Encoder for iPower Motor GM4108H-120T

siqindong, 2021-12-11:
Hi, I bought the[ iPower Motor GM4108H-120T](https://shop.iflight-rc.com/index.php?route=product/product&product_id=217&search=GM4108H-120T) and the encoder AMT103 CUI you used, I found there is no way to mount the encoder to the motor. Any advices?

siqindong, 2021-12-11:
I just bought the [AS5048A Magnetic Encoder](https://shop.iflight-rc.com/as5048a-magnetic-encoder-pro262) for the motor

Closed 2021-12-11.

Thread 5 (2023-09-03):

How to tune the LQR parameters precisely?

weiminshen99, 2023-09-03:
Dear Antun,

Thank you so much for this amazing project and it is very inspiring !!

I made a similar system that is almost working (please see https://youtube.com/shorts/L6I1zPEigmI?feature=share), but I don't know to tune the LQR parameters precisely so to make it completely stabilize.  Could you please give me some advice? Thanks!

-- Wingman

askuric, 2023-09-16:
Hey @weiminshen99 ,

here is a community post from some time ago that might be helpful: https://community.simplefoc.com/t/self-balancing-robot/343/24?u=antun_skuric

Basically, if you have such state space control algorithm:
```
Voltage = k1*angle +k2*angular_velocity +k3*motor_velocity;
```

## tuning procedure

- `k1` and `k2` are necessary for stabilisation, `k3` isn't really. So you can start by setting `k3=0`
- then tune `k1` and `k2`.  In my experience `k1` is more or less 10 times larger `k2`. The expected behavior that you're searching to get is that the robot almost stays upright, but the motor never stops turning. And at some point the motor reaches its maximal velocity and then the robot falls (as it can no longer generate acceleration in that direction)
- Once you've reached this behavior you can  start adding a small value of `k3`.  The `k3` penalizes the motor velocity so the motor will try to stop as soon as it can (as soon as the pendulum is stable and upright).  In my experience the `k3` is around 10 times smaller than `k2`.  With the higher `k3` you will add more importance to the motor velocity so you’ll see the effect visually.
- Now make sure that the sign of the `k3` is good. If you add a small  value `k3` and the pendulum is even more unstable than without it, this probably means that the sign of `k3` is wrong. :smile:

Good luck!

weiminshen99, 2023-09-17:
Hi, Antun,

Thank you so much for your reply and advices! I will try them out and let you know the results.

By the way, the "Self-Balancing Robot" applications are very cool.

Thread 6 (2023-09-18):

Mounting of encoder

DanielFjeld, 2023-09-18:
Hi, i was wandering what part you are using to mount the encoder?
Might just be me who is stupid but I cant see it listed anywhere
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

askuric, 2023-09-19:
Hey @DanielFjeld,

That's a good question.
I've tried many things over the years. The most standard soluiotn I've found is a M4 screw (the longer the better) with couple of nuts (one to secure the screw inside the holow shaft and then two-three to secure the encoder rotor)

In this project however, I've used a male and female screw that is usually used for fixing furniture. For fixing two cabinets together for example. I think is from ikea, but I am not sure any more. I had it lying around.:

It looks something like this:
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

Here is an amazon [link](https://www.amazon.nl/-/en/C41552-MD150/dp/B07RMHDLZH) though I am not sure how long the link with stay alive :smile:

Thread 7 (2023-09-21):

Code error

Alan-lab-ao, 2023-09-21:
Hi, I’m trying to see your project
But, there was an error on the code and i can’t solved it.
I'm sorry, but can I get some help from you?

Alan-lab-ao, 2023-09-21:
![Uploading IMG_6072.jpeg…]()

askuric, 2023-09-21:
PCI listenter is only needed for Arudino UNO, are you using a the UNO board?

Alan-lab-ao, 2023-09-22:
So, i changed to UNO but there’s another error,,,
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

askuric, 2023-09-22:
Hey,
Your photo shows only the warnings, there is no error here.
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

Try finding the "error" word in the log.

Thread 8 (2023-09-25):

swing up code

WONKUK99, 2023-09-25:
HELLO SIR
I'm working on your perfect project.
So far, we have been able to successfully control the reaction wheel by lifting it up and standing it up by hand. However, it is not possible to raise the pendulum upward by swinging up. In your code, 40% of the voltage limit is used for swing-up, but even if I use more than 80%, the pendulum does not reach the top with swing-up.
Currently I am experimenting with the reaction wheel of the same weight and size as the pendulum of your project and a 12V POWER SUPPLY. Are there any expected problems?

Ohhhussama, 2024-03-06:
Hello,

Did you find any solutions for your problem ? Because actually i'm facing the same problem and i don't know what to do

Thank you,

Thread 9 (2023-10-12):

please i need your help

LEEGE0, 2023-10-12:
The motor makes a mechanical sound at first and does not work.
I would appreciate any help in terms of hardware or software.
The Arduino code used is as follows

```#include <SimpleFOC.h>
// software interrupt library
#include <PciManager.h>
#include <PciListenerImp.h>

// BLDC motor init
BLDCMotor motor = BLDCMotor(11);
// driver instance
BLDCDriver3PWM driver = BLDCDriver3PWM(9, 10, 11, 8);
//Motor encoder init
Encoder encoder = Encoder(A1, A2, 500);
// interrupt routine
void doA(){encoder.handleA();}
void doB(){encoder.handleB();}

// pendulum encoder init
Encoder pendulum = Encoder(2, 3, 1000);
// interrupt routine
void doPA(){pendulum.handleA();}
void doPB(){pendulum.handleB();}
// PCI manager interrupt
PciListenerImp listenerPA(pendulum.pinA, doPA);
PciListenerImp listenerPB(pendulum.pinB, doPB);

void setup() {

  // initialise motor encoder hardware
  encoder.init();
  encoder.enableInterrupts(doA,doB);

  // init the pendulum encoder
  pendulum.init();
  PciManager.registerListener(&listenerPA);
  PciManager.registerListener(&listenerPB);

  // set control loop type to be used
  motor.controller = MotionControlType::torque;

  // link the motor to the encoder
  motor.linkSensor(&encoder);

  // driver
  driver.voltage_power_supply = 12;
  driver.init();
  // link the driver and the motor
  motor.linkDriver(&driver);

  // initialize motor
  motor.init();
  // align encoder and start FOC
  motor.initFOC();
}

// loop downsampling counter
long loop_count = 0;

void loop() {
  // ~1ms
  motor.loopFOC();

  // control loop each ~25ms
  if(loop_count++ > 25){
    // updating the pendulum angle sensor
    // NECESSARY for library versions > v2.2
    pendulum.update();
    // calculate the pendulum angle
    float pendulum_angle = constrainAngle(pendulum.getAngle() + M_PI);

    float target_voltage;
    if( abs(pendulum_angle) < 0.5 ) // if angle small enough stabilize
      target_voltage = controllerLQR(pendulum_angle, pendulum.getVelocity(), motor.shaftVelocity());
    else // else do swing-up
      // sets 40% of the maximal voltage to the motor in order to swing up
      target_voltage = -_sign(pendulum.getVelocity())*motor.voltage_limit*0.4;

    // set the target voltage to the motor
    motor.move(target_voltage);

    // restart the counter
    loop_count=0;
  }

}

// function constraining the angle in between -pi and pi, in degrees -180 and 180
float constrainAngle(float x){
    x = fmod(x + M_PI, _2PI);
    if (x < 0)
        x += _2PI;
    return x - M_PI;
}

// LQR stabilization controller functions
// calculating the voltage that needs to be set to the motor in order to stabilize the pendulum
float controllerLQR(float p_angle, float p_vel, float m_vel){
  // if angle controllable
  // calculate the control law
  // LQR controller u = k*x
  //  - k = [40, 7, 0.3]
  //  - x = [pendulum angle, pendulum velocity, motor velocity]'
  float u =  40*p_angle + 7*p_vel + 0.3*m_vel;

  // limit the voltage set to the motor
  if(abs(u) > motor.voltage_limit*0.7) u = _sign(u)*motor.voltage_limit*0.7;

  return u;
}
```
And this is a real picture. Could it be a connection mistake?

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

Jagamu1998, 2023-12-31:
Hi, did you fix that issue, I´m having the same problem. Thanks

Jagamu1998, 2024-01-21:
Hi, in my case I´m using the IFlight-Motor, GM4108H-120T I think it has 11 poles, but I don´t know where to check it.
Probably my issue is occurring because I´m not using the correct size screw for the sensor of the base and does not pick right the data. I will buy a new set of screws in some days.
I don´t think that my motor is damaged because, I did the tests of angle, velocity and torque within the code.

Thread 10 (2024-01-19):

AMT103 Encoder wrong angle

JTShuai, 2024-01-19:
Hi,

I'm using AMT103 encoder for my project as well. I'm here to ask if anyone has the same issue as mine.

I checked the DIP switch of the encoder, it should be the expected PPR number as I set it with the documentation. But still, I cannot get the correct angle value from the sensor.

Hardware: Arduino Uno

When I keep the motor running and get the angle value from the encoder, the value also keeps increasing. But the value is way less than the real angle value. For instance, when the motor rotated half circle, the value I got from the encoder was only around 1 instead of 3.14.

The codes:
```cpp
#include <SimpleFOC.h>

// digital pins
int encoder_pin_a = 3;
int encoder_pin_b = 2;

Encoder encoder = Encoder(encoder_pin_a, encoder_pin_b, 500);
void doA(){encoder.handleA();}
void doB(){encoder.handleB();}

void setup() {
  // initialize encoder hardware
  encoder.init();
  // hardware interrupt enable
  encoder.enableInterrupts(doA, doB);

  // monitoring port
  Serial.begin(9600);
  Serial.println("Setup ready");
  delay(1000);
}

void loop() {
  encoder.update();
  Serial.println(encoder.getAngle());
}
```

JTShuai, 2024-01-20:
Fixed. The issue was the wiring.

Closed 2024-01-20.

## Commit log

2020-05-24 Intial commit
    [bottom_swingup.SLDPRT, bottom_swingup.STEP, bottom_swingup.STL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]
2020-05-24 README images better
    [CUI_amt-102-base-rev-k.sldprt, CUI_amt-102-top-cover-rev-h.sldprt, CUI_amt-hub-bottom-rev-b.sldprt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]
2020-05-24 README half-done docs
    [inverted_inertia_pendulum.SLDASM]
2020-11-24 FIX version 2.0 compliant
    [simplefoc_inverted_pendulim.ino]
